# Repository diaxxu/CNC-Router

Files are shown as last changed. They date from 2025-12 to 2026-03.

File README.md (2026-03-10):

# CNC-Router
<p align="center">
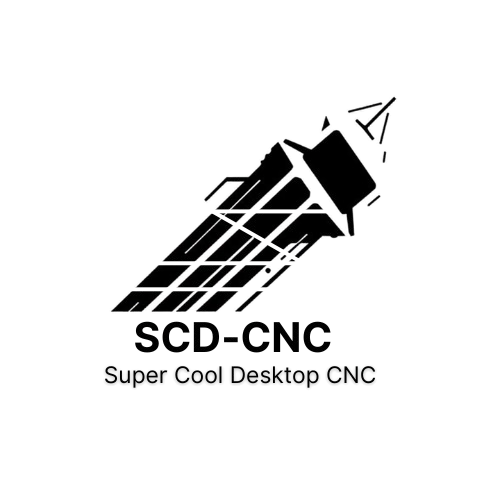
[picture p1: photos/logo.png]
  
</p>

This is my homemade modular CNC machine, built from simple available parts. I designed everything in Fusion 360, researched every component, and chose them carefully. It’s not perfect, but it’s beautiful, and I genuinely enjoyed building it.

## Why I Made This

To get more hands on experience ? this is a very cool project. A CNC that can carve wood and maybe on a good day cut aluminum, isn't that great ?

## 3D Model 

### Front View

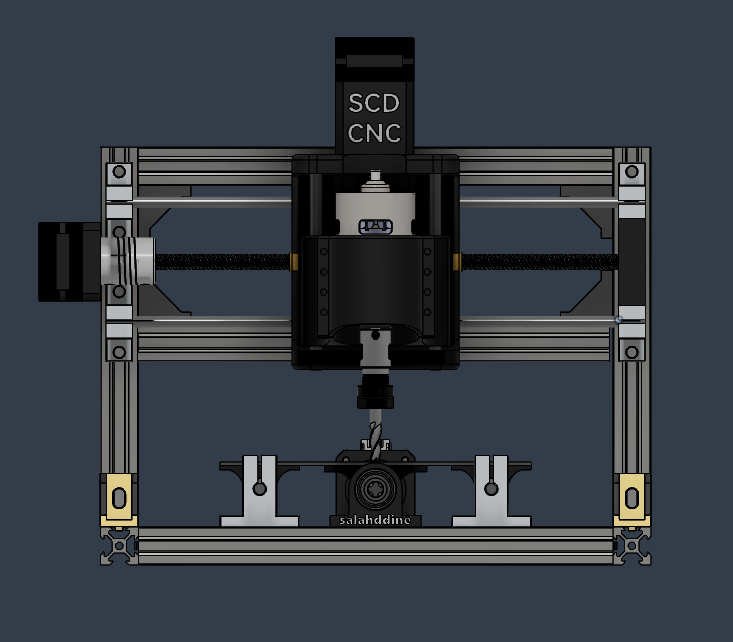
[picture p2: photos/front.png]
Front View


### Side View

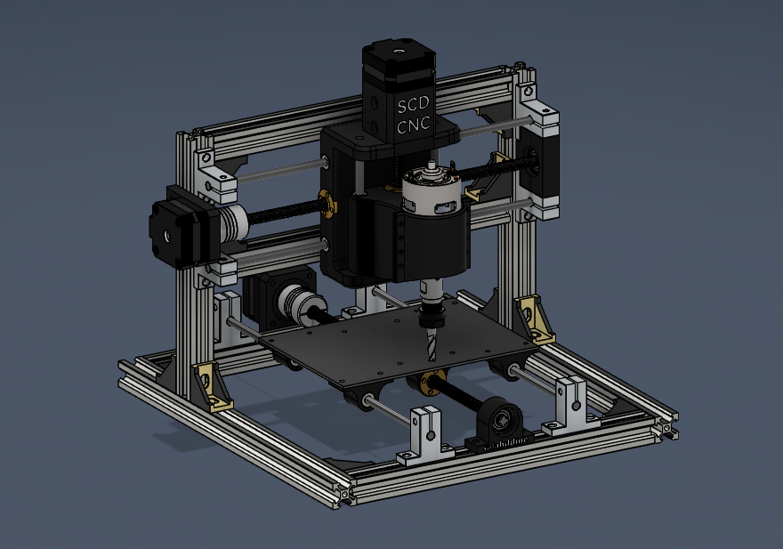
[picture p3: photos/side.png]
Side View


### Full Assembly

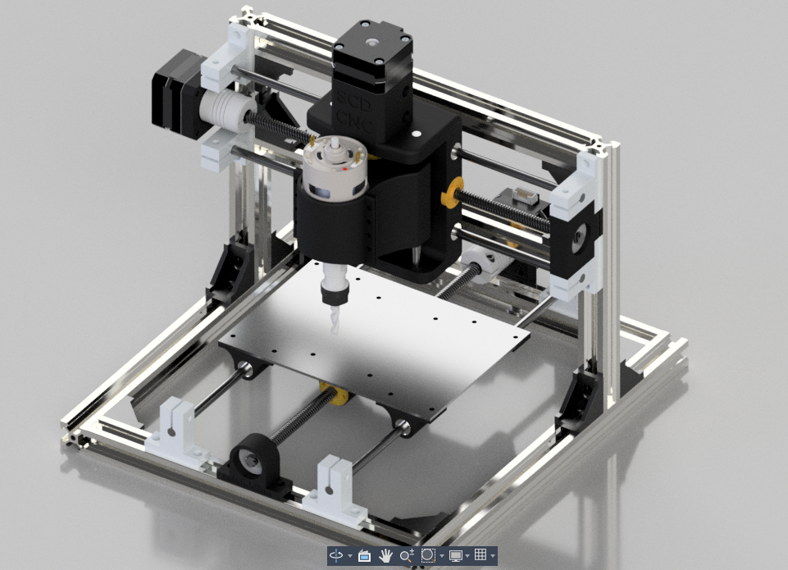
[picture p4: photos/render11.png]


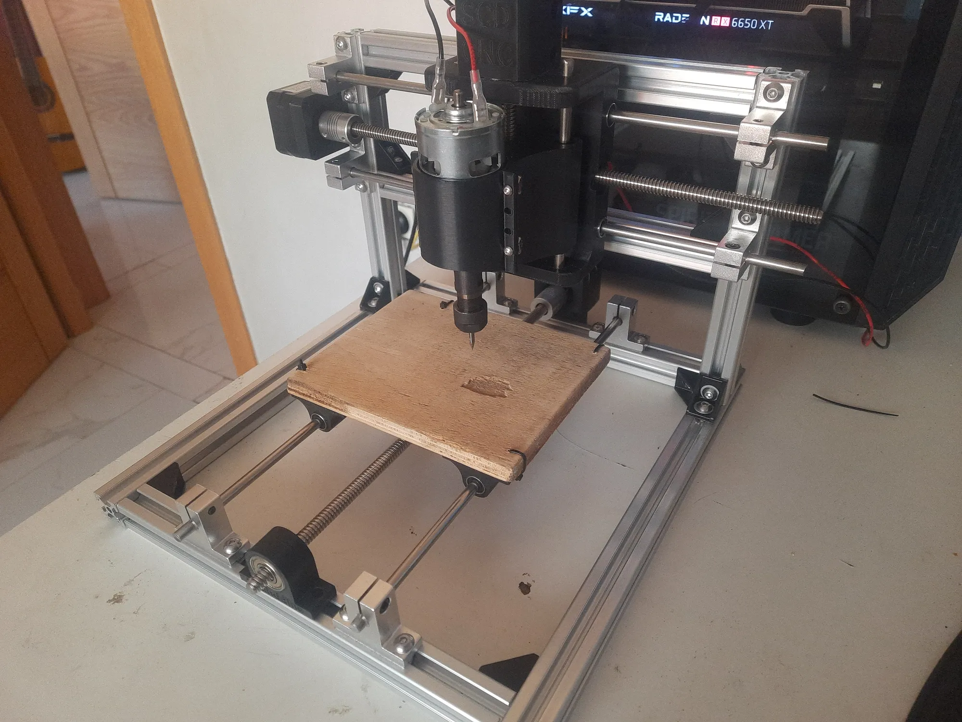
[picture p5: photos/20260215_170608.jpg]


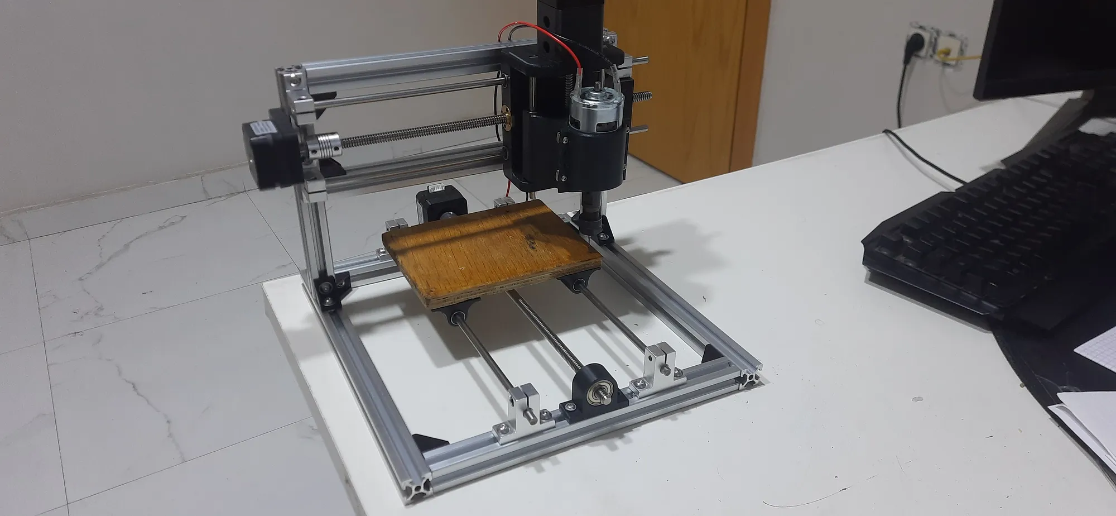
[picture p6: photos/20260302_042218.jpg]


## Schematics and PCB Layout
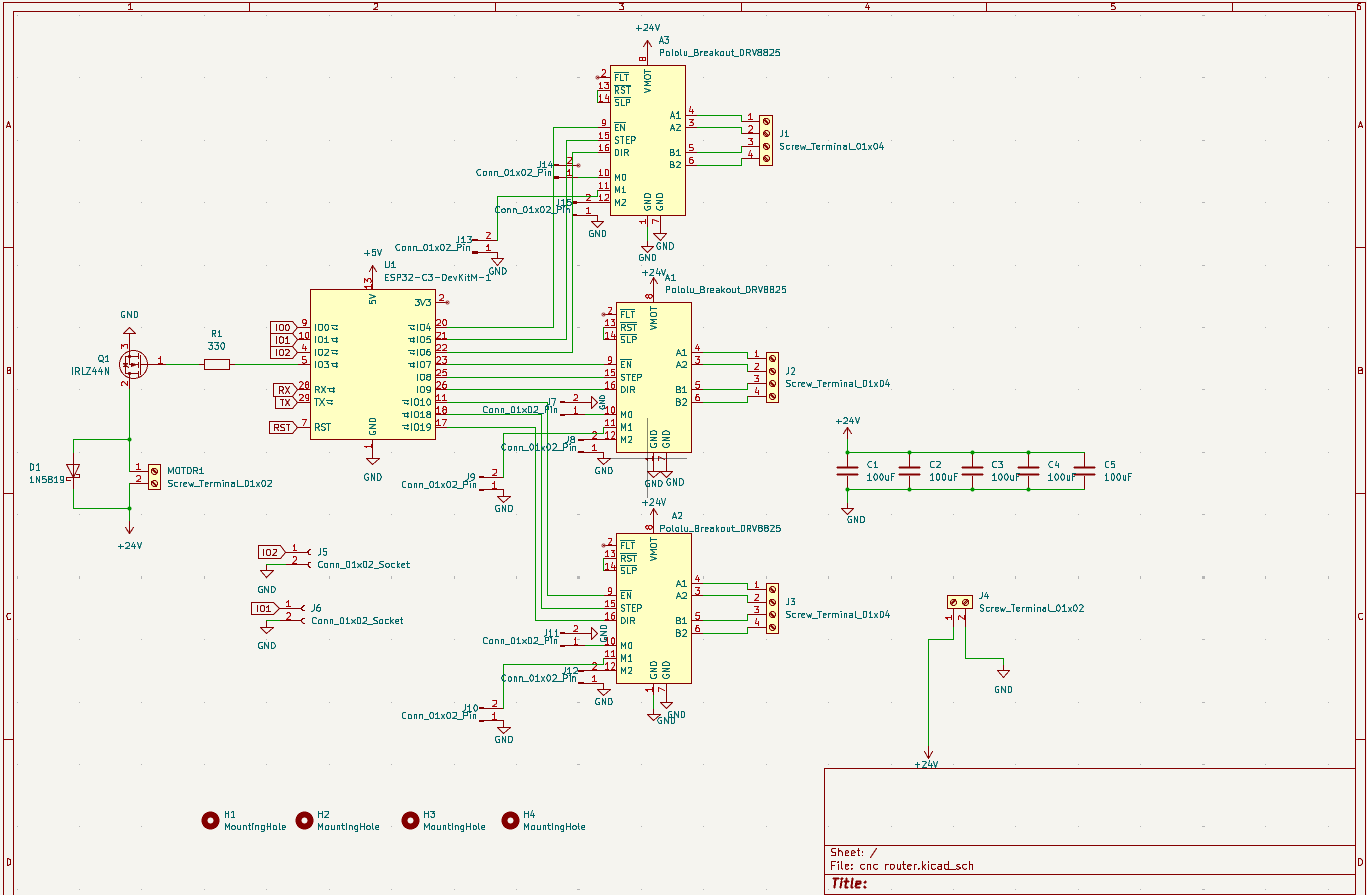
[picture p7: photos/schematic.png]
**made it in Kicad** 
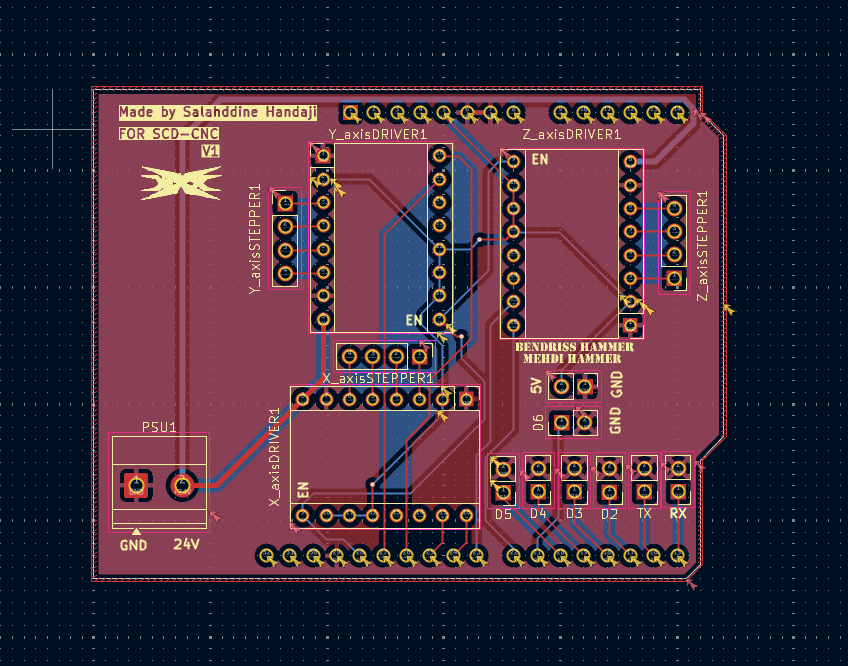
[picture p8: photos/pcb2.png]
Wiring Diagram

(i re-routed this 5 or 6 times 😭) </br>
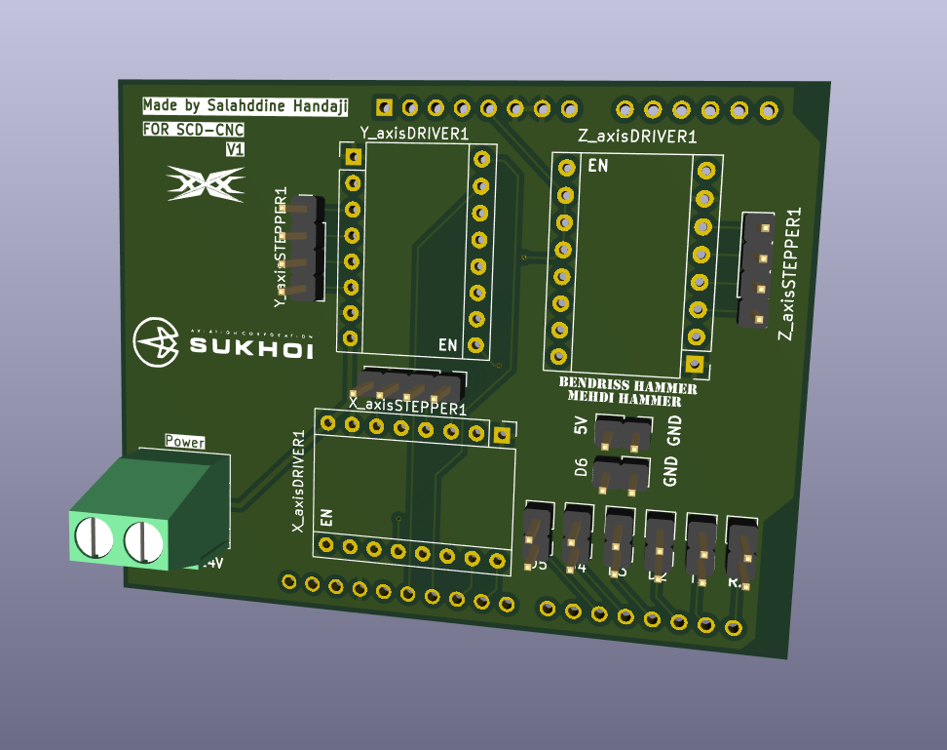
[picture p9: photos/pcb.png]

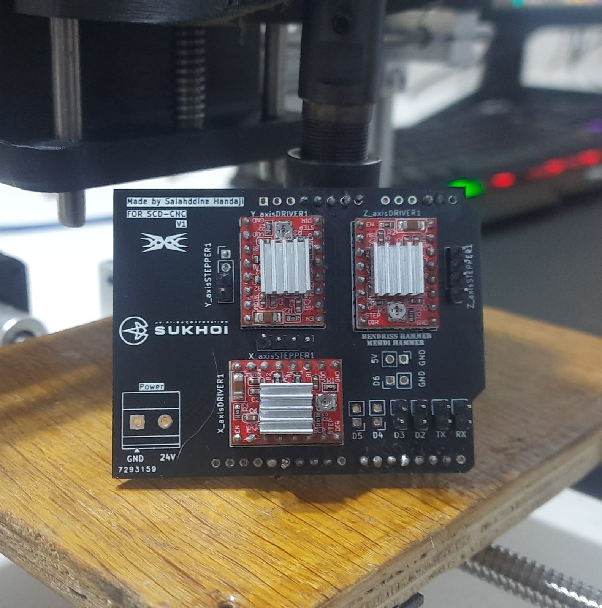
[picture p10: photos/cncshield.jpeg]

im really bad at soldering :c </br>
### Schematic ( wire diagram ) 
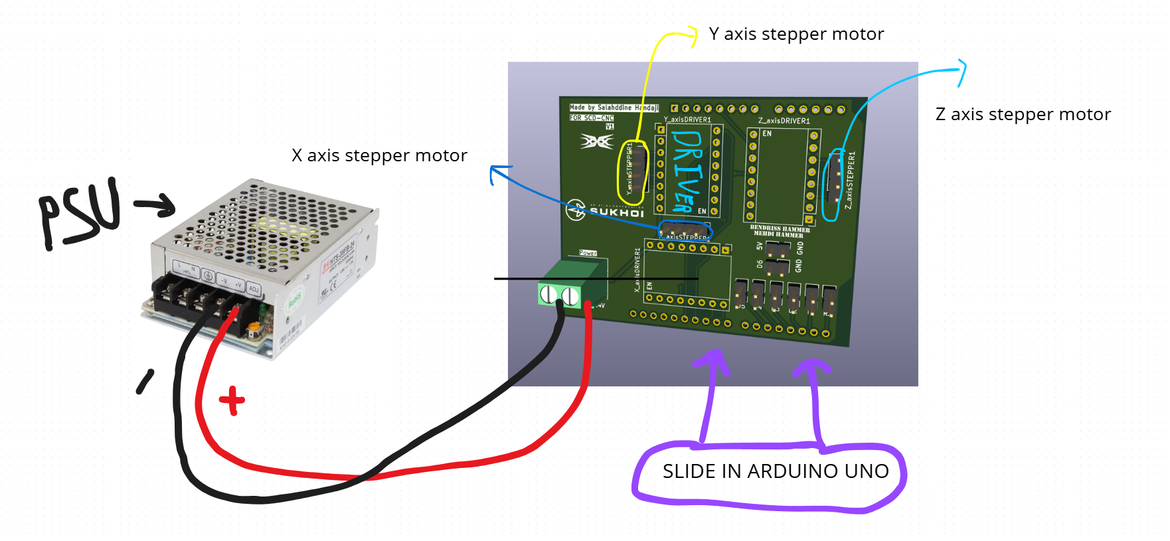
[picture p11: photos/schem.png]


## Firmware Installation 
1- assemble your driver board ( put the driver in plane ) Insert it into the Arduino Uno header <br/>
2- connect the arduino uno your pc<br/> 
3- download grbl.zip from the github <br/>
4- upload the code <br/>
5- install Universal Gcode sender <br/>
6- learn CAM software or use Easel <br/>
7- enjoy the results <br/>

## BOM (Bill of Materials)

Here is the secret sauce!!

| Item | Quantity | Unit | link|
| --- | --- | ---- | --- |
| T8 Lead Screw 2mm lead 500 mm (with nut) | 1 | pcs  | https://www.aliexpress.com/item/1005007457419235.html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 |
| T8 screw round | 10 | pcs  |  https://www.aliexpress.com/item/1005007438925484.html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 |
| LM6UU linear bearing | 4 | pcs  |  https://www.aliexpress.com/item/1005007791097936.html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 |
| NEMA17 stepper motor | 3 | pcs  | https://www.aliexpress.com/item/1005003874936862.html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 |
| M5 T-nut for 2020 extrusion | 100 | pcs  | https://www.aliexpress.com/item/1005007805744044.html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 |
| Shaft decoupler | 5 | pcs  | https://www.aliexpress.com/item/1005006031199563.html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 |
| Limit switch (mechanical) | 5 | pcs  | https://www.aliexpress.com/item/1005010111182286.html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 | 
| Smooth shaft ~8mm x 500mm | 2 | pcs  | https://www.aliexpress.com/item/1005006104915821.html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 |
| 2020 T-slot extrusion 300mm | 4 | pcs  | https://www.aliexpress.com/item/1005002652962344.html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 |
| Emergency stop button | 1 | pcs  | https://www.aliexpress.com/item/4000144892605.html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 |
| Spindle | 1 | pcs  | https://www.aliexpress.com/item/1005006435477384.html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 |
| 4 flute HRC65 end mill | 4 | pcs  | https://www.aliexpress.com/item/1005006112116580.html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 |
| Esp-32 wroom32 |  1 | pcs  | https://www.aliexpress.com/item/1005007117977294.html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 |
| Capacitor 100uF | 40 | pcs | https://www.aliexpress.com/item/1005007792451411.html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 |
| DRV8825 |5 | pcs | https://www.aliexpress.com/item/1005006199405206.html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 |
| irlz44n |10 | pcs | https://www.aliexpress.com/item/32895956089.html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 |
| 1N5819 |50 | pcs | https://www.aliexpress.com/item/1005001552094086.html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 |
| Screw terminal |10 | pcs | https://www.aliexpress.com/item/1005001677869988.html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 |
| Pin headers 1*40pin |10 | pcs | https://www.aliexpress.com/item/32980998451.html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 |
| PSU 24V 16A |1 | pcs | https://www.aliexpress.com/item/1005003962776196.html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|
| pcb cost | 5 | pcs |  https://www.allpcb.com/cart?protype=2&upfileid=797791 |
| 3d printing cost | 456 | grams |  fusion estimation |
### Total 
- in Mad : 3.512 </br>
- in Dollar : 384.72

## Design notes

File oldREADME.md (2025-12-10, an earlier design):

# CNC-Router

This is my homemade CNC machine. It started as an idea and slowly turned into a full mission . I designed everything in Fusion 360, with 3d printed brackets. i also researched the parts, and carefully choosed components. I’m not calling it perfect, its **beautiful** and i like it  .

## Why I Made This

To get more hands on experience ? this is a very cool project. A CNC that can carve wood and maybe on a good day cut aluminuim, isn't that great ?

## 3D Model 

### Front View

Front View

### Side View

Side View

### Top View

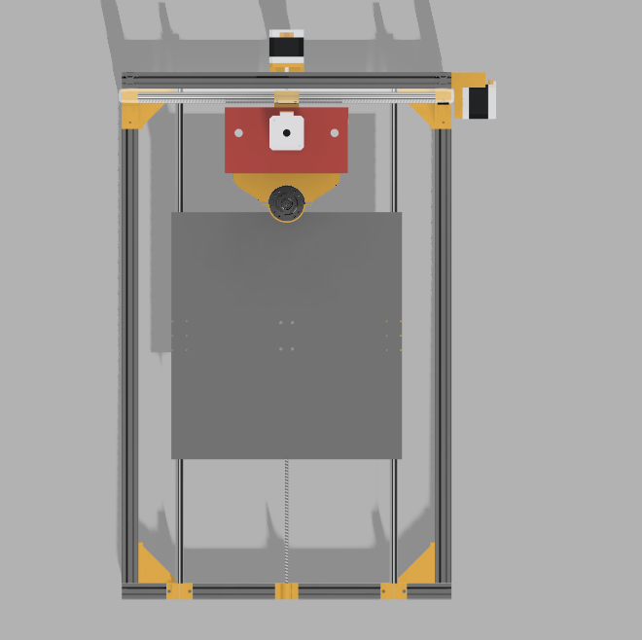
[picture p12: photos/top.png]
Top View


### Full Assembly

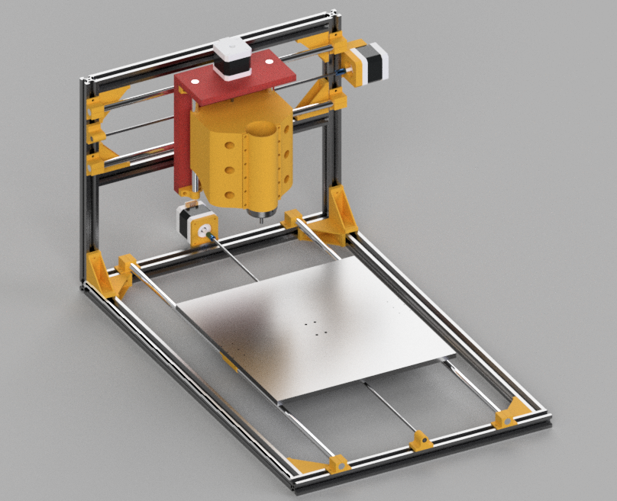
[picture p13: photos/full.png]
Full Assembly


This is quite long, maybe I should make it shorter
## Wiring Diagram

still didn't start this phase so y'all gonna need to wait !

Wiring Diagram

## BOM (Bill of Materials)

Here is the secret sauce!!

| Item | Quantity | Unit | Notes |
| --- | --- | ---- | --- |
| T8 Lead Screw 2mm lead 500 mm (with nut) | 1 | pcs  | One per axis; anti-backlash recommended |
| T8 screw round | 10 | pcs  | |
| LM8UU linear bearing | 4 | pcs  | Two per platform |
| NEMA17 stepper motor | 3 | pcs  | |
| M5 T-nut for 2020 extrusion | 100 | pcs  | |
| Shaft decoupler | 5 | pcs  | One per lead screw |
| Limit switch (mechanical) | 5 | pcs  | X+/X-, Y+/Y-, Z+/Z- |
| Smooth shaft ~8mm x 500mm | 2 | pcs  | Works with LM8UU |
| 2020 T-slot extrusion 300mm | 4 | pcs  | |
| Emergency stop button | 1 | pcs  | |
| Spindle | 1 | — | |
| 4 flute HRC65 end mill | 4 | — | |

More things will probably get added because that’s how these builds go. But for now, this is the heart of the machine.

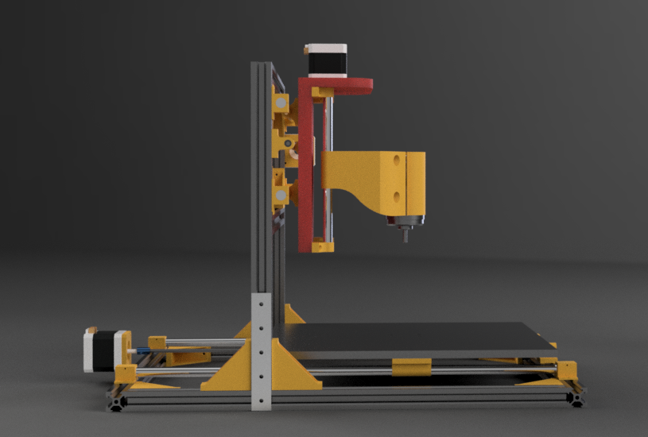
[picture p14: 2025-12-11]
Render/Capture d'écran 2025-12-11 201720.png

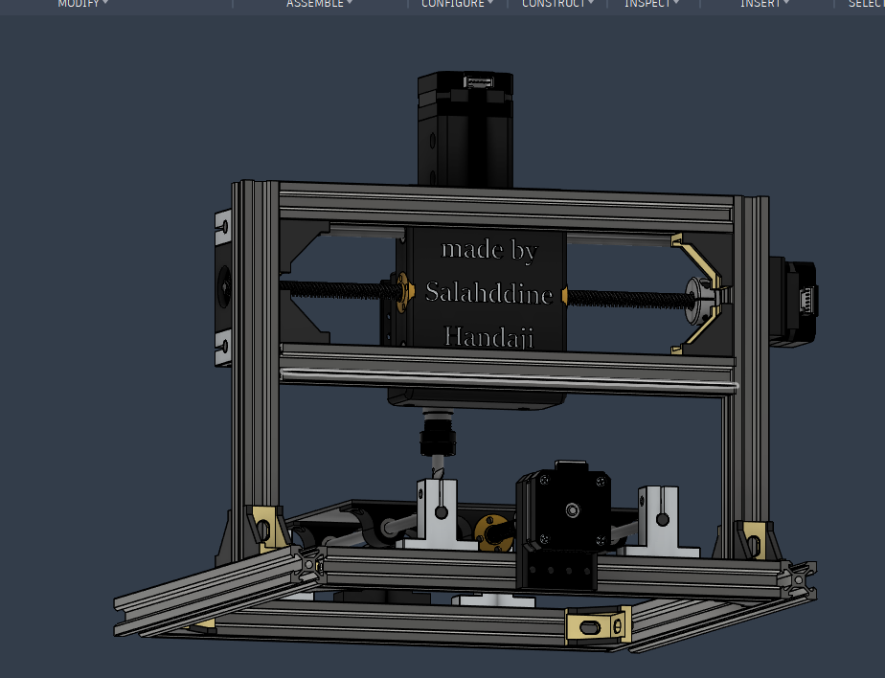
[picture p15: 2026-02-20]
photos/back.png

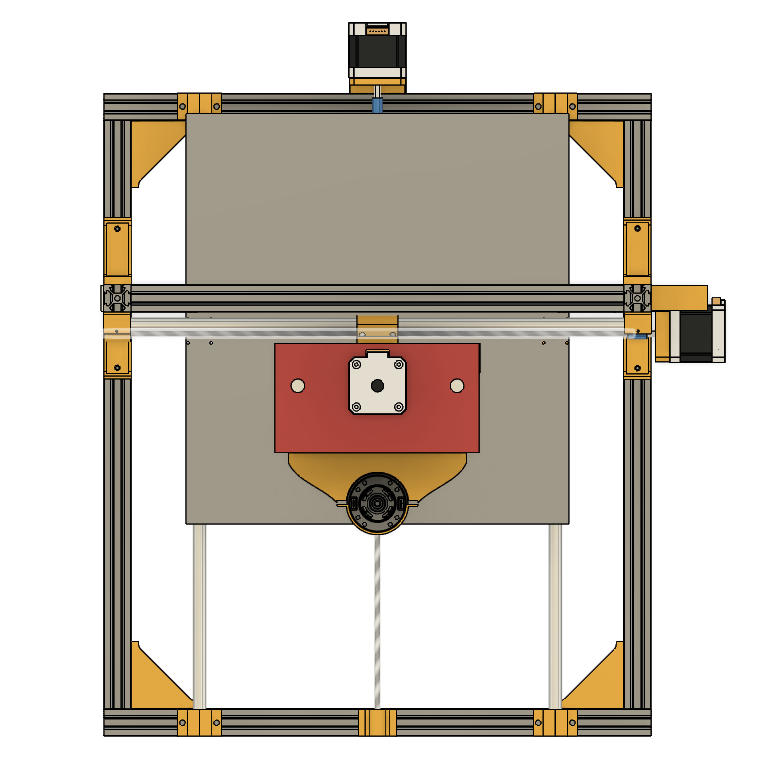
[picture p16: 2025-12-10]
photos/top1.png

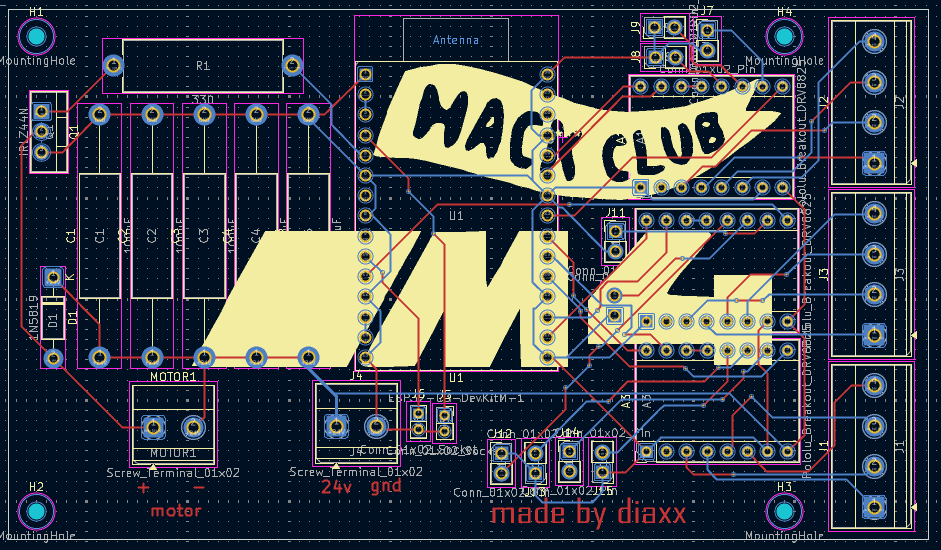
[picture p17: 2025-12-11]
photos/layout.png

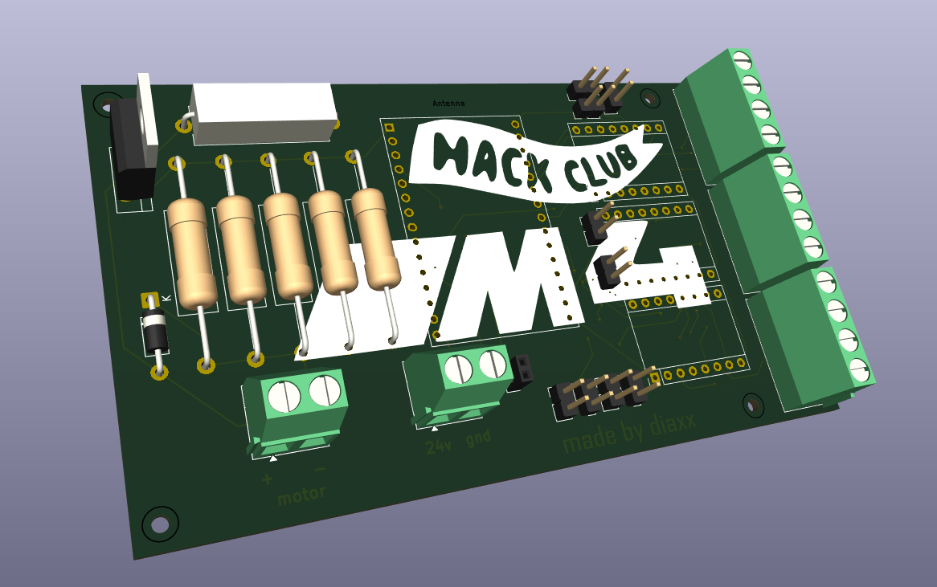
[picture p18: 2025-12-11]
photos/3dview.png

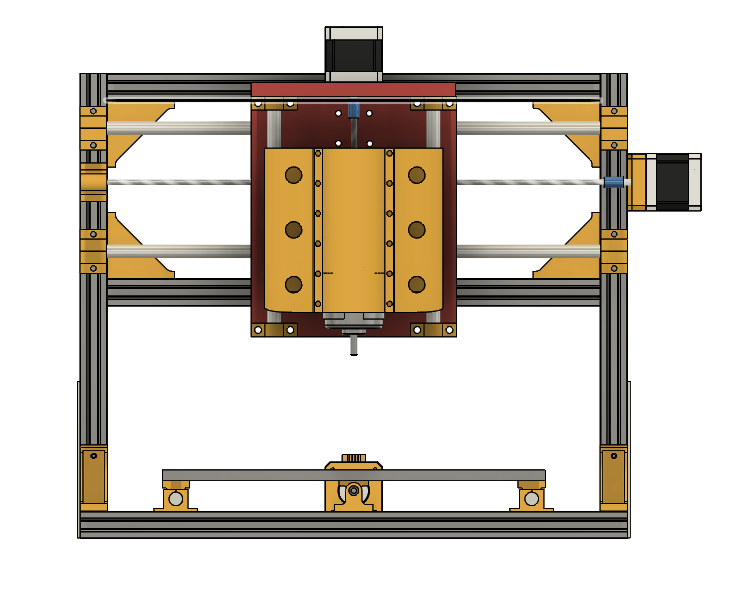
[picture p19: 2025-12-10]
photos/front1.png

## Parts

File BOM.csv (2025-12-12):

Item | Quantity | Unit | price(in mad) | price (in $dollar) | link
T8 Lead Screw 2mm lead 500 mm (with nut) | 1 | pcs | 67.8 | 7.32 | https://www.aliexpress.com/item/1005007457419235.html
T8 screw round | 10 | pcs | 46.65 | 5.04 | https://www.aliexpress.com/item/1005007438925484.html
LM8UU linear bearing | 4 | pcs | 42.8 | 4.63 | https://www.aliexpress.com/item/1005007791097936.html
NEMA17 stepper motor | 3 | pcs | 240 | 25.92 | https://www.aliexpress.com/item/1005003874936862.html
M5 T-nut for 2020 extrusion | 100 | pcs | 76.77 | 8.3 | https://www.aliexpress.com/item/1005007805744044.html
Shaft decoupler | 5 | pcs | 71.52 | 7.73 | https://www.aliexpress.com/item/1005006031199563.html
Limit switch (mechanical) | 5 | pcs | 29.73 | 3.21 | https://www.aliexpress.com/item/1005010111182286.html
Smooth shaft ˜8mm x 500mm | 2 | pcs | 134 | 14.47 | https://www.aliexpress.com/item/1005006104915821.html
2020 T-slot extrusion 300mm | 4 | pcs | 273 | 29.48 | https://www.aliexpress.com/item/1005002652962344.html
Emergency stop button | 1 | pcs | 36 | 3.89 | https://www.aliexpress.com/item/4000144892605.html
Spindle | 1 | pcs | 282 | 30.46 | https://www.aliexpress.com/item/1005006435477384.html
4 flute hrc65 end mill | 4 | pcs | 29.73 | 3.21 | https://www.aliexpress.com/item/1005006112116580.html
Esp-32 wroom32 | 1 | pcs | 18.86 | 2.04 | https://www.aliexpress.com/item/1005007117977294.html
Capacitor 100uF | 40 | pcs | 135.35 | 14.62 | https://www.aliexpress.com/item/1005007792451411.html
DRV8825 | 5 | pcs | 45.88 | 4.95 | https://www.aliexpress.com/item/1005006199405206.html
irlz44n | 10 | pcs | 9.87 | 1.07 | https://www.aliexpress.com/item/32895956089.html
1N5819 | 50 | pcs | 9.87 | 1.07 | https://www.aliexpress.com/item/1005001552094086.html
Screw terminal | 10 | pcs | 83.08 | 9.04 | https://www.aliexpress.com/item/1005001677869988.html
Pin headers 1×40 pin | 10 | pcs | 14.56 | 1.58 | https://www.aliexpress.com/item/32980998451.html
PSU 24V 16A | 1 | pcs | 373.8 | 40.4 | https://www.aliexpress.com/item/1005003962776196.html

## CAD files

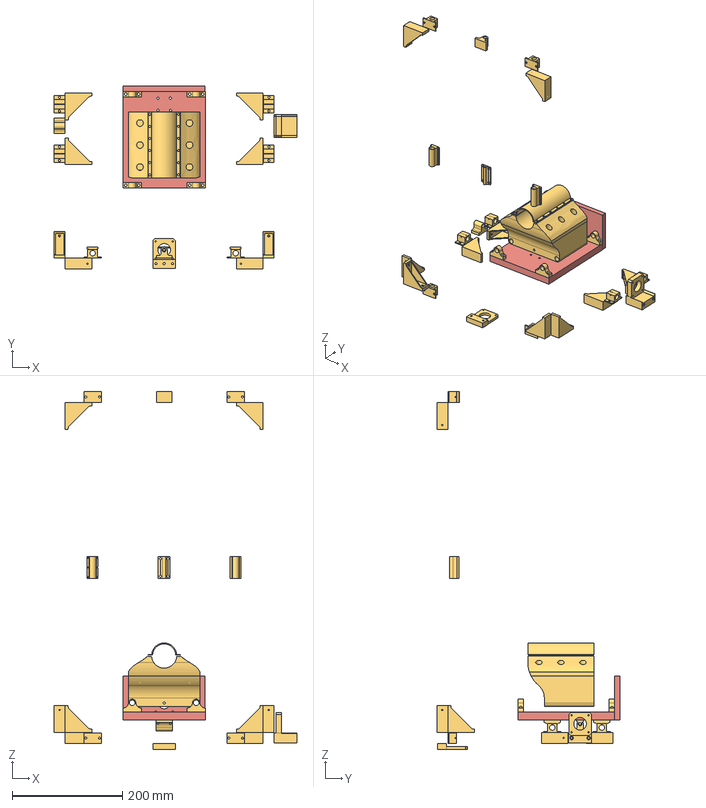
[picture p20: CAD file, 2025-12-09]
CAD/3d printables/3d printable .step
441.5 x 333.3 x 650.9 mm

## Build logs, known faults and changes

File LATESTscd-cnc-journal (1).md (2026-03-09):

<!--
  This journal is auto generated by Hack Club Blueprint.
-->

# 12/8/2025 5 PM - making the base   

_Time spent: 3.0h_  

Hi ! I started by designing the base of my CNC mill/plotter in Fusion 360 , I used 20×20 T-slot aluminum extrusion. The frame measures about 239.5 × 200 mm, and I added 3D-printed brackets to hold everything firmly in place

# 12/8/2025 7:01 PM - Added the x movement  

_Time spent: 1.0h_  

so I designed a 3D-printed shaft-support brackets to hold the two guide rods for the X-axis. They keep the rods aligned, and I’ll add the platform next.Capture d'écran 2025-12-08 185943

# 12/8/2025 7:43 PM - FINISHED THE PLATFORM  

_Time spent: 0.4h_  

SO I finally added the platform added the platform everything going well For now  hopefully i design the y axis in the next hour hopefully but i would still need 3d models of some component like the spindle , the extrusion etc   

# 12/8/2025 8:00 PM - Z axis  

_Time spent: 0.4h_  

 made the Z axis structure i just used the same component next goal is to make the Z platform where will be the Y axis and the spindle or the module or whatever ... 

# 12/8/2025 8:52 PM - Y axis  

_Time spent: 1.2h_  

Me again I’ve finished designing the platform for the Z-axis, and now I’m moving on to modeling the Y-axis for my CNC mill/plotter project this where i will make it **modular**  

# 12/8/2025 10 PM - finished the design   

_Time spent: 2.0h_  



after 2 hours i finally finished making this cnc milling machine im so exhausted + i need to recheck those stepper motor and their support . tomoroww i will try to make the controller, the github repo and the BOM   

# 12/9/2025 9 AM - WHOLE REMAKE  

_Time spent: 12.0h_  

I didn't like it cuz it was so small SO i stayed all night making this cnc router thats now modular just swap the head !! its better its bigger and _yellow_ which is also cool. ill make a bom and a repo !  Capture d'écran 2025-12-09 085522
Capture d'écran 2025-12-09 074643 
Capture d'écran 2025-12-09 085506

# 12/9/2025 12 PM - made the bom and repo   

_Time spent: 2.5h_  

just created a repo for this project added a readme.md , the cad files ( with the full assembly ) and Bill Of Material next task is probably making the electronics  full

# 12/10/2025 5 PM - changed the layout   

_Time spent: 9.0h_  

I shortened the frame to save money and i reinforced the Y axis extrusion with a 20mm plate since i changed the whole layout the dimensions now are 469*400mm   
### plate moving 



# 12/10/2025 8 PM - finishing touches   

_Time spent: 3.0h_  

i made some final changes to the design ( fillets etc... ) also changed the readme.md . Now i can hop onto the next task making the pcb 
### the final design 

### bare bone 

### the 3d printed components


# 12/11/2025 2 AM - made the cnc shield 1  

_Time spent: 6.0h_  

I researched the available drivers and chose the DRV8825 because it handles higher current and offers finer microstepping. I finished the schematic, then routed the PCB. It took me three attempts, but I eventually settled on this design. i will probably upgrade or even change it since i m not a big fan of the layout nor screw terminal this took so much time i know its simple but im not that good in electrical engineering.
### schematics

### pcb layout
Capture d'écran 2025-12-11 023922
### 3d view


# 12/11/2025 7 AM - some change to the shield  

_Time spent: 5.0h_  

Added proper 2-pin connector for adjusting the micro-stepping  then made 2 socket pin for the limit switch mod. Also added a screw terminal for the big emergency stop button so it can cut the 24V line instantly. Makes the CNC safer and way less sketchy.



# 12/11/2025 9 AM - fixed the repo   

_Time spent: 3.0h_  


made a logo using canva and enlarged the bom then added the price in dollar and mad 
made a name for this project, updated the cad file  ( SCD-CNC which stand for Super Cool Desktop CNC) 

# 12/11/2025 12 PM - firmware   

_Time spent: 3.0h_  

the cnc is going to run Grbl _ Esp32 firmware i added it in the repo 
added pin configuration ( pins_scdc.h ) in the firmware folder 
also added the gerber of the cnc shield  from kicad 

# 12/11/2025 8 PM - some change   

_Time spent: 8.0h_  

### PCB

- Cleaned up the layout  and added proper mounting holes so the board can be fixed down 
- added some arts (m4 and blueprint logo)


### Repo

- Made a KiCad folder and added the Gerber files. Tweaked the CAD folder too(screws , brackets and lead screw nut). Also added a new PCB section in the README.md so everything look Nicer .
- added a whole render folder in the repo 
- researched a PSU since i forgot about it then added it to the BoM



# 12/11/2025 9 PM - PSU case   

_Time spent: 2.0h_  

### RENDER OF BOTH THE CNC AND PSU 


> this look fire

### THE CASE  
Made a 3D-printed power supply case in Fusion 360 and mounted it on the CNC. It actually came out looking really good!!  I dropped the STL into the repo under the 3D-printable folder so it’s all organized. 
 

# 12/11/2025 11 PM - Controlling Grbl_ESP32  

_Time spent: 1.0h_  

I’ll be controlling the CNC through **Universal G-Code Sender**. The whole setup will be accessible through a Web-UART interface, so I can run it directly from a browser without needing a dedicated PC.  


# 12/12/2025 12 PM - Working on modularity  

_Time spent: 6.0h_  

I added a laser module to the machine. Swapping between the milling head and the laser head is really easy:

**1.Remove the four mounting screws.**


**2.Take off the spindle and the 3D-printed front cover.**

**3.Place the laser module in position and secure it using the four screw holes**


**4.install the 3D-printed cover.**


### And just like that. The machine is ready for engraving.

# 12/12/2025 2 PM - Last touches (hopefully)  

_Time spent: 2.0h_  

### - Repo 
- Added links in BoM section (Readme.md)
- Included links in BOM.csv
- Implemented the full journal.md
- Improved the README :D

---

### Please reviewer, could I get tickets instead of a grant? I’m in a tough spot with exams and spent all of this week building this CNC.  (i really need to lock in)
 Capture d'écran 2025-12-11 201554
3D printer here i come (:

# 12/13/2025 - Re clarification   

_Time spent: 1.0h_  

As I said I'm not going to build this I only want those tickets not a grant ( for 3d printer) because I have so much going on please just give me those tickets 🙏😭Screenshot_20251213-093831_GitHub

# 12/29/2025 - re-reclarification  

_Time spent: 0.5h_  

i will re submit this project since tickets now are not given unless you build your project physically so i will try to get grants to build it and make it in real life Capture d'écran 2025-12-11 210428

# 1/24/2026 - buying the parts   

_Time spent: 4.0h_  

After a lot of troubleshooting, I finally managed to place my order. exciting, right? I’m expecting to receive it between February 11 and 20. 
## stay tuned! 

# 2/8/2026 3 PM - Edit  

_Time spent: 1.0h_  

## shipping
90% of the components arrived today. I'm still waiting for some to arrive to start the Assembly of the SCD CNC i hope everything go smoothlyCapture d'écran 2025-12-11 201554

# 2/8/2026 7 PM - fixed the cnc shield  

_Time spent: 4.0h_  

well i totally re-designed the cnc shield to be able to slide in the arduino furthermore i also added some cool decal i sent it to get manufactured at ALL pcb Capture d'écran 2026-02-08 182516

# 2/9/2026 10 AM - Major Changes  

_Time spent: 15.0h_  

After talking with a professional CAD designer, I was told the same thing that Samliu mentioned as well 3D-printed components are too weak unless you increase their size or switch to a different material.
So I decided to replace the parts that were judged inadequate, and I spent the entire night redesigning the cnc. 



# 2/9/2026 5 PM - lubricating the linear bearing   

_Time spent: 3.0h_  

i received the linear bearing (lm6uu) and they fit perfectly on the 6mm shaft 7 of them glide great but the last 3 are rough (probably defective) I tried lubricating them and saw a minor improvement ill see if i can do something if not i will re-order 3 replacement ):Capture d'écran 2026-02-09 104317
LMM__92137

# 2/10/2026 - The 3d printed part arrived   

_Time spent: 4.6h_  

I just received the 3d printed components but when I tried to press fit the linear bearing ... well guess 11.9mm was too small so I spent 1h sanding. 
The 608zz bearing was fitted easily since I knew the diameter. Im still waiting for some ali express part to arrive 

# 2/13/2026 - last delivery scheduled tomorrow   

_Time spent: 1.0h_  

i received 99% of the component i only need 2 more to start assembly i need the 6mm shaft support that will holder the platform and the round screws and thats it tomorrow i will go cut all the metal to their respective size and start to assemble 

# 2/15/2026 - Assembly   

_Time spent: 13.0h_  

I received all the components and started the assembly process. It didn’t begin smoothly. I had to search everywhere for long M3 screws (which felt impossible to find). Eventually, I found someone selling them locally. I also went to a workshop where I cut all my rods and aluminum extrusions to the correct dimensions.

IMG-20260215-WA0002

---

## Base Frame Assembly

I started by assembling the base frame. The T-slot screws were extremely difficult to tighten properly I probably spent nearly an hour just to make sure the base was securely fastened.

IMG-20260215-WA0005

IMG-20260215-WA0018

---

## Vertical Extrusion Assembly

Next, I assembled the vertical aluminum extrusion that supports the Z-axis structure.

IMG-20260215-WA0023

---

## Z-Carriage Assembly

I then assembled the Z-carriage. This step went very smoothly it is probably my best designed part of the entire build.

IMG-20260215-WA0025

---

## Z-Axis Linear Shaft Installation

I installed the 6mm end shaft supports, inserted the 6mm linear shafts, and carefully slid the Z-carriage into place.

IMG-20260215-WA0034

---

## Stepper Motor Mounting (Z-Axis)

I mounted the stepper motor using the 3D-printed support bracket.

IMG-20260215-WA0027

At this stage, the entire top assembly was completed.



---

## Lead Screw & Final Shaft Support Assembly

Next, I mounted the end shaft support (SK6), installed the 6mm shaft, and assembled the lead screw with the stepper motor and its 3D-printed mount.

IMG-20260215-WA0031

---

## Final Frame Integration

Finally, I mounted the completed top assembly onto the base frame.



---

That concludes the work completed for this day.

I still need to find or order the correct lead screw nut, since I mistakenly ordered the wrong pitch. I will try to source it locally; otherwise, I will reorder it from AliExpress. I also need to mount the moving platform.

## more pics 





# 2/17/2026 - Mounting the platform and running the cnc   

_Time spent: 5.0h_  

For the platform, I cut some wood that I had laying around then sanded it. As of now I only have 2 axis working I tested them the lead screw had some run-out but I fixed it now I only need 1 nut for the lead screw to hopefully finish this project 🙏 😭 


# 2/20/2026 2 PM - First Gcode run  

_Time spent: 8.0h_  

After I finally got the last piece I needed for my CNC, I mounted it onto the Y-axis platform and started working on the electronics. WhatsApp Image 2026-02-20 at 13.34.00WhatsApp Image 2026-02-20 at 13.34.00 (1)

I plugged everything in carefully and made sure the polarity was correct because I didn’t want to fry anything on the first try. Once everything was connectedWhatsApp Image 2026-02-20 at 13.33.59

, I made a simple circle in G-code just to test the machine.
WhatsApp Image 2026-02-20 at 13.33.58

It went really bad. The movement was shaky and messy, and it didn’t look anything like a circle. So I started checking everything one by one. I noticed the platform was kind of loose and was jumping while moving, so I tightened it. Then I realized the vertical aluminum extrusion wasn’t fully secure either. After that, I basically tightened the whole machine. Almost every bolt needed more tightening.

After doing that, the machine felt way more solid. The vibrations were reduced a lot, and it moved smoother. I’d say it improved the rigidity by around 30%. When I tested it again, it was clearly better.

Then I designed a crescent moon shape and ran it. The result was okay. Not perfect, but definitely not terrible either. It was good enough to see that the machine was improving.WhatsApp Image 2026-02-20 at 13.33.57WhatsApp Image 2026-02-20 at 13.33.56 (1)

Later, I removed the 775 spindle motor and replaced it with a pen to test plotting instead of cutting. I just wanted to see the motion without worrying about cutting forces. When I ran the program, it actually drew a circle properly. 
That felt really good because it showed that the movement system was finally working the way it should.

With that final test done and the circle coming out clean, I can officially call this project complete. Everything runs the way it should, the structure is solid, and the motion is smooth. It started as a pile of parts and problems, but now it’s a fully working machine.

Mission accomplished. Ready to ship.
CAD

# 2/20/2026 10 PM - Improvements  

_Time spent: 4.0h_  

So you want to make this cnc here are some suggestions i would give you :
- instead of using 6mm shaft **use 8 or bigger diameter shafts** 
- The LM6UU linear bearings I ordered are very small, which makes them difficult to work with during manufacturing and increases the chances of ending up with a non-functional result. I would recommend using larger bearings or switching entirely to linear rails for better reliability 
- More infill on 3d printed parts i recommend printing with 40% infill
- Use 40x40 aluminium extrusion 
- sturdier z axis carriage 

all these suggestions would improve the SCD-CNC milling quality :>

Screenshot_20260220-225118_Gallery

# 3/2/2026 - Getting things to work better  

_Time spent: 14.0h_  

After quite a lot of tightening screws I decided to replace the spoilboard with something more beautiful and straight it did require some sanding not gonna lie I then bought some wood screw and decided to replace the plastic zippers fixing the Y platform guess what, Rigidity improved(duh) the play in the Y axis is now less than 1mm I also oiled up 😭 the bearings, shafts and the lead screws for smoother ride also had the z axis not fixed it was glued but now it's properly tightened with screw i believe the play in the z axis is the biggest ( 2.5-3mm) because I only have 2 linear bearing instead of 4 well that's it  





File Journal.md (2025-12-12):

# Journal

## Working on modularity

### 2025-12-12 - 1.0 hour
I added a laser module to the machine. Swapping between the milling head and the laser head is really easy:

1. Remove the four mounting screws.
2. Take off the spindle and the 3D-printed front cover.
3. Place the laser module in position and secure it using the four screw holes.
4. Install the 3D-printed cover.

And just like that, the machine is ready for engraving.

---

## Controlling Grbl_ESP32

### 2025-12-12 - 2.0 hours
I’ll be controlling the CNC through Universal G-Code Sender. The whole setup will be accessible through a Web-UART interface, so I can run it directly from a browser without needing a dedicated PC.

---

## PSU case

### 2025-12-12 - 8.0 hours
Render of both the CNC and PSU

This looks fire.

**The Case**
Made a 3D-printed power supply case in Fusion 360 and mounted it on the CNC. It actually came out looking really good. I dropped the STL into the repo under the 3D-printable folder so it’s all organized.

---

## Some change

### 2025-12-11 - 3.0 hours

### PCB

Cleaned up the layout and added proper mounting holes so the board can be fixed down. Added some arts (M4 and blueprint logo).

### Repo

Made a KiCad folder and added the Gerber files. Tweaked the CAD folder too (screws, brackets and lead screw nut). Also added a new PCB section in the README.md so everything looks nicer. Added a whole render folder in the repo. Researched a PSU since I forgot about it then added it to the BoM.

---

## Firmware

### 2025-12-11 - 3.0 hours
The CNC is going to run Grbl_ESP32 firmware. I added it in the repo, added pin configuration (pins_scdc.h) in the firmware folder, and added the Gerber of the CNC shield from KiCad.

---

## Fixed the repo

### 2025-12-11 - 5.0 hours

### Logo

Made a logo using Canva and enlarged the BoM, then added the price in dollar and MAD. Made a name for this project and updated the CAD file (SCD-CNC which stands for Super Cool Desktop CNC).

---

## Some change to the shield

### 2025-12-11 - 6.0 hours
Added proper 2-pin connectors for adjusting micro-stepping, then made two socket pins for the limit switch mod. Also added a screw terminal for the big emergency stop button so it can cut the 24V line instantly. Makes the CNC safer and way less sketchy.

---

## Made the CNC shield 1

### 2025-12-11 - 3.0 hours
I researched the available drivers and chose the DRV8825 because it handles higher current and offers finer microstepping. I finished the schematic, then routed the PCB. It took me three attempts, but I eventually settled on this design. I’ll probably upgrade or even change it since I’m not a big fan of the layout nor the screw terminal. This took so much time; I know it’s simple but I’m not that good in electrical engineering.

---

## Finishing touches

### 2025-12-10 - 9.0 hours
Made some final changes to the design (fillets, etc.) and changed the README.md. Now I can hop onto the next task: making the PCB.

---

## Changed the layout

### 2025-12-09 - 2.5 hours
I shortened the frame to save money and reinforced the Y-axis extrusion with a 20mm plate. Since I changed the whole layout, the dimensions are now 469 × 400 mm.

---

## Made the BoM and repo

### 2025-12-09 - 12.0 hours
Created a repo for this project, added a README.md, the CAD files (with full assembly), and the Bill of Materials. Next task is probably making the electronics.

---

## Whole remake

### 2025-12-08 - 2.0 hours
I didn’t like it because it was too small, so I stayed up all night making this CNC router that’s now modular — just swap the head. It’s better, bigger, and yellow, which is also cool. I’ll make a BoM and a repo.

---

## Finished the design

### 2025-12-08 - 1.2 hours
After two hours I finally finished making this CNC milling machine. I’m exhausted and I need to recheck the stepper motors and their supports. Tomorrow I’ll try to make the controller, the GitHub repo, and the BoM.

---

## Y axis

### 2025-12-08 - 0.4 hours
Finished designing the platform for the Z-axis, now moving on to modeling the Y-axis for the CNC mill/plotter project. This is where I will make it modular.

---

## Z axis

### 2025-12-08 - 0.4 hours
Made the Z-axis structure using the same components. Next goal is to make the Z platform where the Y-axis and the spindle/module will be mounted.

---

## Finished the platform

### 2025-12-08 - 1.0 hour
Finally added the platform. Everything is going well for now. Hopefully I’ll design the Y-axis in the next hour, but I still need 3D models of some components like the spindle and the extrusion.

---

## Added the X movement

### 2025-12-08 - 3.0 hours
Designed 3D-printed shaft-support brackets to hold the two guide rods for the X-axis. They keep the rods aligned, and I’ll add the platform next.

---

## Making the base

### 2025-12-08 - 2.0 hours
Started by designing the base of the CNC mill/plotter in Fusion 360 using 20×20 T-slot aluminum extrusion. The frame measures about 239.5 × 200 mm, and I added 3D-printed brackets to hold everything firmly in place.

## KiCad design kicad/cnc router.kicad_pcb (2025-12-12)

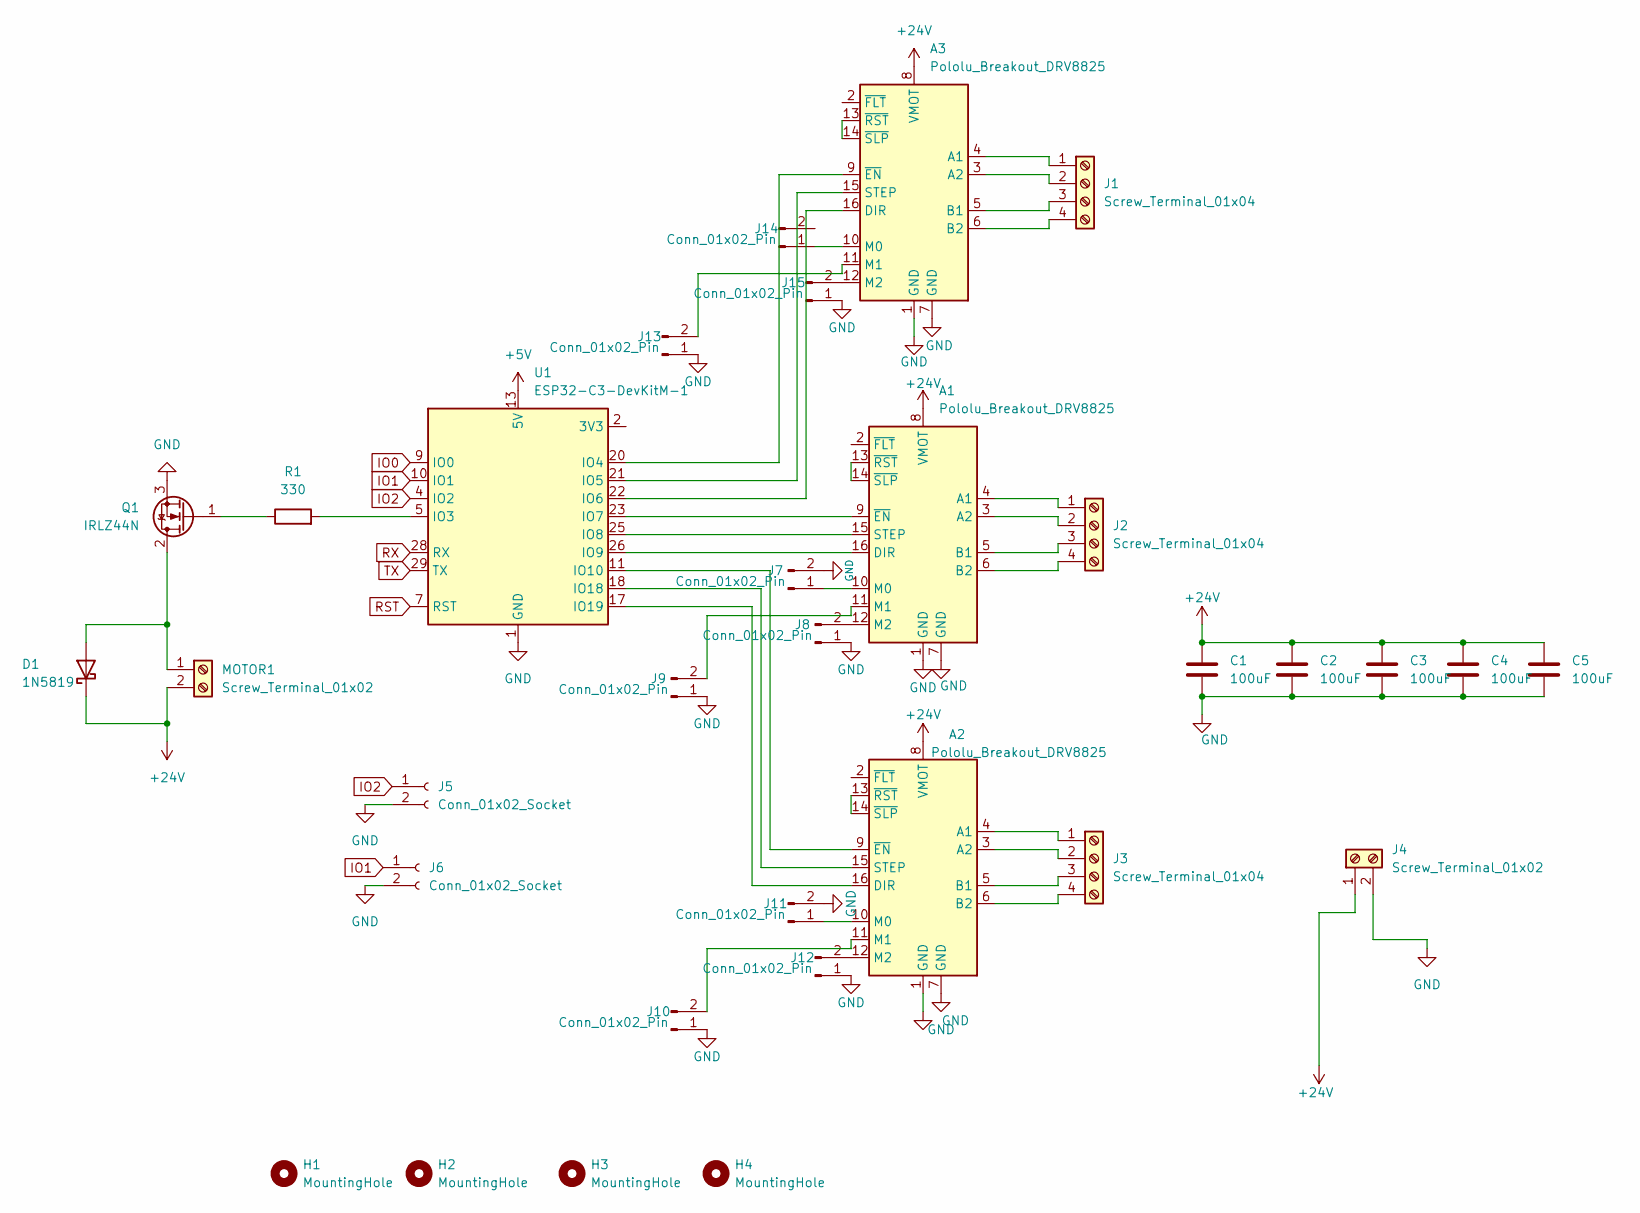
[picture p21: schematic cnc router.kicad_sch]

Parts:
A1, A2, A3: Pololu_Breakout_DRV8825; Pololu_Breakout-16_15.2x20.3mm
C1, C2, C3, C4, C5: 100uF; R_Axial_DIN0516_L15.5mm_D5.0mm_P30.48mm_Horizontal
D1: 1N5819; D_DO-41_SOD81_P10.16mm_Horizontal
H1, H2, H3, H4: MountingHole; MountingHole_2.1mm
J1, J2, J3: Screw_Terminal_01x04; TerminalBlock_Phoenix_MKDS-1,5-4-5.08_1x04_P5.08mm_Horizont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
J4: Screw_Terminal_01x02; TerminalBlock_Phoenix_MKDS-1,5-2_1x02_P5.00mm_Horizontal
J5, J6: Conn_01x02_Socket; PinSocket_1x02_P2.00mm_Vertical
J7, J8, J9, J10, J11, J12, J13, J14, J15: Conn_01x02_Pin; PinHeader_1x02_P2.54mm_Vertical
MOTOR1: Screw_Terminal_01x02; TerminalBlock_Phoenix_MKDS-1,5-2_1x02_P5.00mm_Horizontal
Q1: IRLZ44N; TO-220-3_Vertical
R1: 330; R_Axial_Power_L20.0mm_W6.4mm_P22.40mm
U1: ESP32-C3-DevKitM-1

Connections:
+5V: U1.13 (5V), U1.14 (5V)
+24V: A1.8 (VMOT), A2.8 (VMOT), A3.8 (VMOT), C1.1, C2.1, C3.1, C4.1, C5.1, D1.1 (K), J4.1, MOTOR1.2
GND: A1.1 (GND), A1.7 (GND), A2.1 (GND), A2.7 (GND), A3.1 (GND), A3.7 (GND), C1.2, C2.2, C3.2, C4.2, C5.2, J4.2, J5.2, J6.2, J7.2, J8.1, J9.1, J10.1, J11.2, J12.1, J13.1, J15.1, Q1.3 (S), U1.1 (GND), U1.6 (GND), U1.8 (GND), U1.12 (GND), U1.15 (GND), U1.16 (GND), U1.19 (GND), U1.24 (GND), U1.27 (GND), U1.30 (GND)
IO0: U1.9 (IO0)
IO1: J6.1, U1.10 (IO1)
IO2: J5.1, U1.4 (IO2)
unnamed: A1.4 (A1), J2.1
unnamed: A1.3 (A2), J2.2
unnamed: A1.5 (B1), J2.3
unnamed: A1.6 (B2), J2.4
unnamed: A1.16 (DIR), U1.26 (IO9)
unnamed: A1.10 (M0), J7.1
unnamed: A1.11 (M1), J9.2
unnamed: A1.12 (M2), J8.2
unnamed: A1.15 (STEP), U1.25 (IO8)
unnamed: A1.9 (~EN), U1.23 (IO7)
unnamed: A1.13 (~RST), A1.14 (~SLP)
unnamed: A2.4 (A1), J3.1
unnamed: A2.3 (A2), J3.2
unnamed: A2.5 (B1), J3.3
unnamed: A2.6 (B2), J3.4
unnamed: A2.16 (DIR), U1.17 (IO19)
unnamed: A2.10 (M0), J11.1
unnamed: A2.11 (M1), J10.2
unnamed: A2.12 (M2), J12.2
unnamed: A2.15 (STEP), U1.18 (IO18)
unnamed: A2.9 (~EN), U1.11 (IO10)
unnamed: A2.13 (~RST), A2.14 (~SLP)
unnamed: A3.4 (A1), J1.1
unnamed: A3.3 (A2), J1.2
unnamed: A3.5 (B1), J1.3
unnamed: A3.6 (B2), J1.4
unnamed: A3.16 (DIR), U1.22 (IO6)
unnamed: A3.10 (M0), J14.1
unnamed: A3.11 (M1), J13.2
unnamed: A3.12 (M2), J15.2
unnamed: A3.15 (STEP), U1.21 (IO5)
unnamed: A3.9 (~EN), U1.20 (IO4)
unnamed: A3.13 (~RST), A3.14 (~SLP)
unnamed: D1.2 (A), MOTOR1.1, Q1.2 (D)
unnamed: Q1.1 (G), R1.1
unnamed: U1.2 (3V3), U1.3 (3V3)
unnamed: R1.2, U1.5 (IO3)
RST: U1.7 (RST)
RX: U1.28 (RX)
TX: U1.29 (TX)

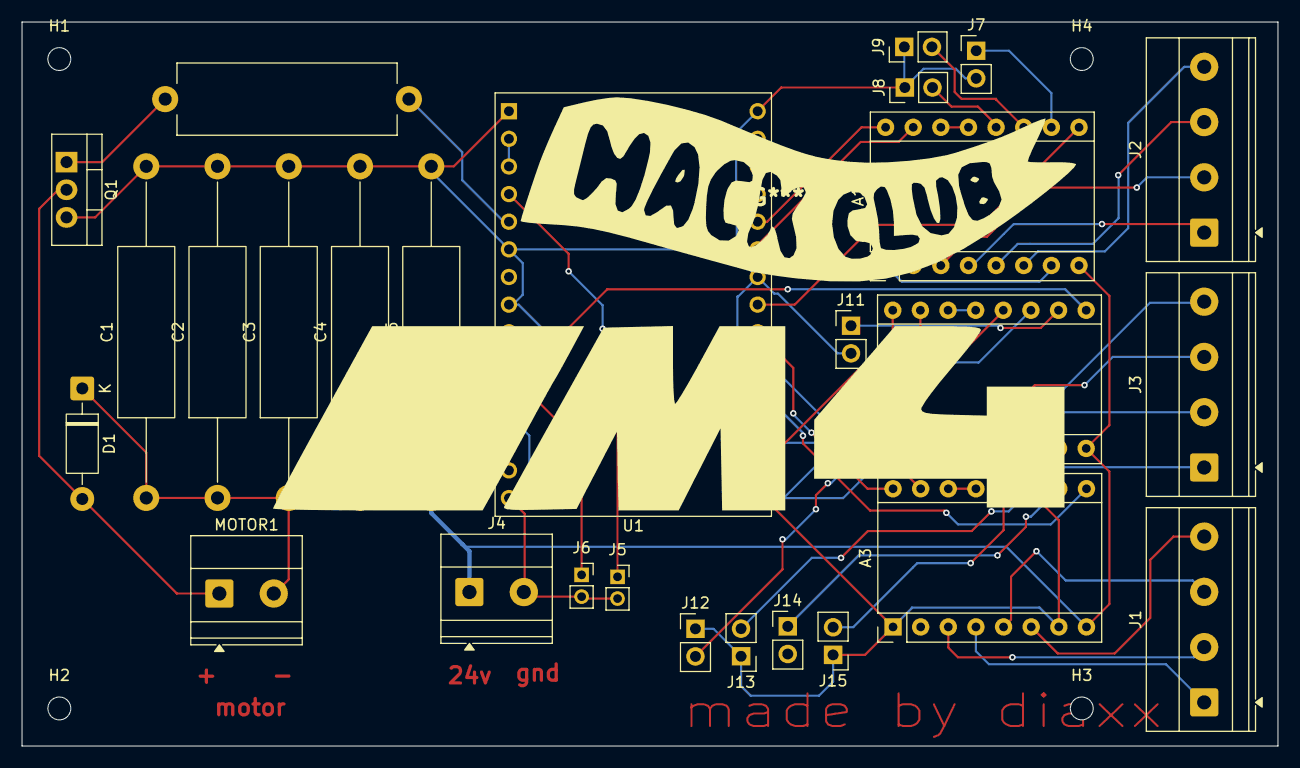
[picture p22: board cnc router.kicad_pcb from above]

Board: 2 copper layers, 115.4 x 66.5 mm, 32 parts (0 on the bottom side), 42 nets.

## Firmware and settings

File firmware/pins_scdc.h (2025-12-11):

// pins_scdc.h
// Pin mapping for SCDCNC ESP32 Shield
// Compatible with GRBL_ESP32

#define X_STEP_PIN     5
#define X_DIR_PIN      6
#define X_ENABLE_PIN   4

#define Y_STEP_PIN     8
#define Y_DIR_PIN      9
#define Y_ENABLE_PIN   7

#define Z_STEP_PIN     18
#define Z_DIR_PIN      19
#define Z_ENABLE_PIN   10

#define SPINDLE_ENABLE_PIN 3
#define SPINDLE_PWM_PIN    3

#define LIMIT_X_PIN    2
#define LIMIT_Y_PIN    1

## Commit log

2025-12-09 Update README to clarify BOM section
2025-12-10 Add old README for CNC Router project
    This README provides an overview of a homemade CNC router project, including its purpose, 3D models, wiring diagram, and a bill of materials.
2025-12-11 Add pricing details to BOM in README
    Updated BOM to include pricing in MAD and USD.
2025-12-11 Add pin mapping for SCDCNC ESP32 Shield
2025-12-11 Fix image paths and enhance schematic section
    Updated image paths and improved formatting for schematics.
2025-12-11 Rename a powersupply.step to PSU_case.step
    [PSU_case.step]
2025-12-12 Add product links to BOM in README
    Added links to BOM items for easy access.
2025-12-29 Update README with PCB and 3D printing costs
    Added PCB and 3D printing cost details to the README.
2026-03-04 Update README with schematic and cost details
    Added schematic image and updated cost explanation.
2026-03-04 Add firmware installation section and update BOM
    Added firmware installation instructions and updated BOM with new items.
2026-03-10 Update README with CNC shield image and soldering note
    Added a CNC shield image and a note about soldering skills.
